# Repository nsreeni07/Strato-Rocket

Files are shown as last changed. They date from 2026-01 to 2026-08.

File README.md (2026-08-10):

Description

Strato is my first mid-power rocket, built as an introduction to rocketry and aerospace engineering. It stands 1.1 meters tall, reaches about 560 meters in altitude, and travels up to Mach 0.4. The rocket includes onboard avionics for GPS tracking, altitude measurement, and flight video recording.

The flight computer is a LILYGO T-Beam (ESP32-based) that logs GPS and telemetry data. A BMP390 measures altitude throughout the flight. An ESP32-CAM with an OV2640 records onboard video. The rocket uses a 36-inch parachute deployed by a black powder charge for safe recovery.

How to Use

Before launch, assemble the motor, recovery system, and avionics. Power on the flight computer and confirm GPS lock and sensor readings. After launch, the system automatically records flight data and deploys the parachute at apogee. After landing, retrieve the rocket and download the recorded data and video.

Why I Made This Project

I built Strato to begin my journey into rocketry and aerospace engineering. I wanted hands-on experience with avionics, sensors, telemetry, and recovery systems. This project helped me develop practical engineering skills and build a foundation for more advanced rockets in the future.

IMG_0525 (1)







|Category |Name |Price |Source |Purpose |FIELD6|Quantity|FIELD8|
|---|---|---|---|---|---|---|---|
|Electronics |LILYGO T-Beam V1.1(915mhz)|$66.64|https://lilygo.cc/en-us/products/t-beam?variant=51708943335605 |1 for rocket, 1 for ground tracking. | |2 | |
| |ESP32-CAM + Antenna |$5.82 |https://www.aliexpress.us/item/3256808866325459.html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 |The camera Board | |1 | |
| |OV2640 Camera |$4.23 |https://www.aliexpress.us/item/3256802853835121.html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 |To record the flight | |1 | |
| |MicroSD Card (32GB) |$3.55 |https://www.aliexpress.us/item/3256806229393591.html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 |Store Flight Video | |1 | |
| |BMP390 |$3.45 |https://www.aliexpress.us/item/2255800994181054.html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 |To measure altitude. | |1 | |
| |18650 Battery |$10.35|https://www.aliexpress.us/item/3256808362166008.html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 |Power for the rocket and ground station. | |1 | |
| |28 AWG Silicone Wire |$7.41 |https://www.aliexpress.us/item/3256808281675998.html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 |Vibration-proof wiring. | |1 |k |
| |Dupont Lines |$6.18 |https://www.aliexpress.com/item/3256806675662297.html |Breadboard Connector Wire | |1 | |
| | | | | | | | |
|Category |Name |Price |Source |Purpose | |Quantity| |
|Hardware |Epoxy |$3.48 |https://www.aliexpress.us/item/3256806928842047.html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|Adhesive | |2 | |
| |Recovery Wadding |$5.99 |https://estesrockets.com/products/recovery-wadding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 |Parachute Protection during ejection charge| |1 | |
| |Parachute Materials |$17.99|https://estesrockets.com/products/rip-stop-parachute?_pos=1&_sid=acb6b3712&_ss=r&variant=51539308052785 |Brings Rocket down safely | |1 | |
| |M6 Eye Bolts 30mm |$0.99 |https://www.aliexpress.us/item/3256803591110349.html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 |For attaching Shock cords to main Body | |1 | |
| |M6 Nylon Hex Spacers |$0.99 |https://www.aliexpress.us/item/2251832781404540.html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 |To Seperate wires and PCBS | |1 | |
| |Main Body Tube |$16.38|https://locprecision.com/products/slotted-cardboard-airframes?variant=39778658582719 |Body Tube | |1 | |
| |Shock Cord |$9.15 |https://locprecision.com/products/shock-cords?variant=39778658058431 |Absorbs shock | |1 | |
| |Mounting Tube |$2.25 |https://locprecision.com/products/motor-mount-tubing?variant=39778656813247 |Hold engine | |1 | |
|Category |Name |Price |Source |Purpose | |Quantity| |
|Self-Bought |G78G-7 |$0.00 |Buying Myself |Rocket Motor | |1 | |
| |Solder |$0.00 |Buying Myself |To solder wires to Avionics | |1 | |
| |3d Printed Nose Cone |$0.00 |Buying Myself |Nose Cone | |1 | |
| |3d Avionics Bay |$0.00 |Buying Myself |Hold Electronics | |1 | |
| |Spray Paint |$0.00 |Buying Myself |To Paint Rocket | |1 | |
| |PVC 5-Way |$0.00 |Buying Myself |For Rocket Launch Stand | |1 | |
| |Wood Filler |$9.99 |https://www.amazon.com/gp/product/B07JPB64XH/ref=ewc_pr_img_1?smid=A3I7U6FHIJ15X2&psc=1 |To thicken Epoxy | |1 | |
| |Balsa Wood |$7.99 |https://www.amazon.com/gp/product/B096P4G1RR/ref=ewc_pr_img_8?smid=A3BTZYV8IYFCZ9&th=1 |To Make Engine Centering Rings and Fins | |1 | |
| | | | | | | | |
| | | | | | | | |
| | | | | | | | |
| | | | | | | | |
| | | | | | | | |
| | | | | | | | |
| | | | | | | | |
| | | | | | | | |
| | | | | | | | |
| | | | | | | | |
|Below Totals contain Tax and Shipping | | | | | | | |
| | | | | | | | |
|Lilygo Total |$82.64 | | | | | | |
|Aliexpress Total |$51.59 | | | | | | |
|Amazon Total |$0.00 | | | | | | |
|LOC Total |$40.99 | | | | | | |
|Estes Total |$33.07 | | | | | | |
| | | | | | | | |
| | | | | | | | |
|Grant Total: |$208.29 | | | | | | |

[Strato BOM - Sheet1 (3).csv](https://github.com/user-attachments/files/25199135/Strato.BOM.-.Sheet1.3.csv)

# Strato-Rocket
https://docs.google.com/spreadsheets/d/1U2yEqBZTKHJVJrxIfUGXRck5QNupb0Gcpo2Jn2H-yjM/edit?usp=sharing

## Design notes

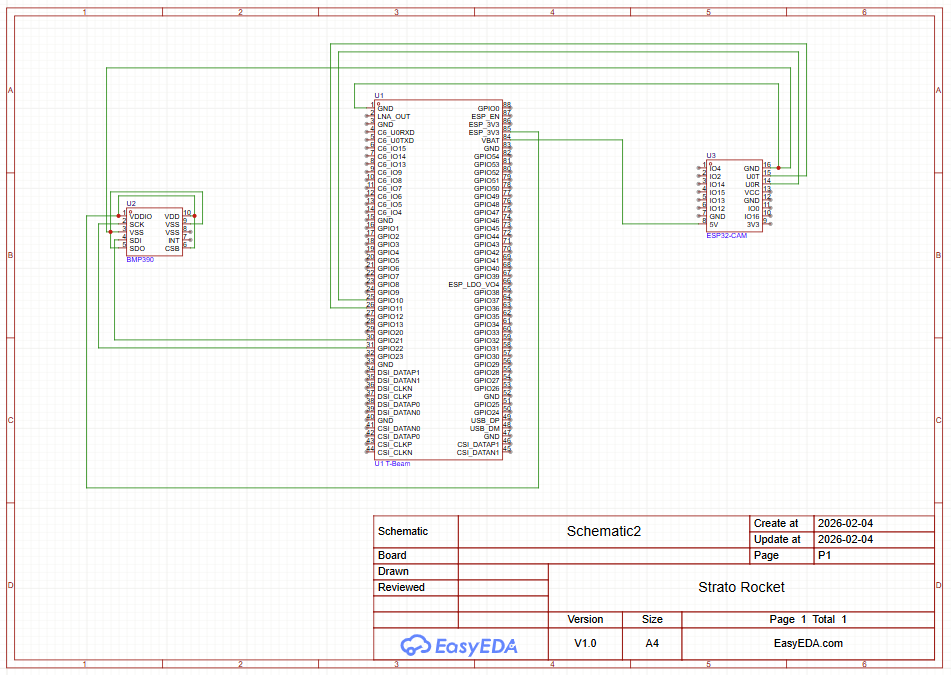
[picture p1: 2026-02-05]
Design Files/Strato-Avionics-Schematic.png

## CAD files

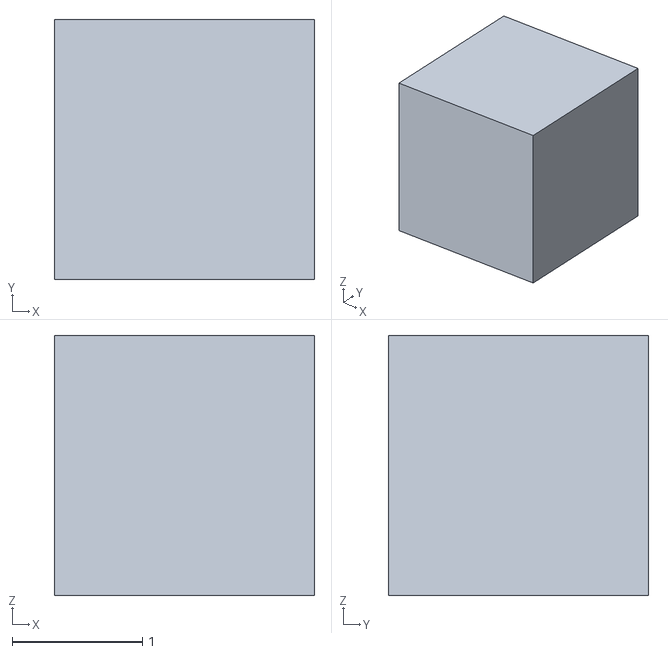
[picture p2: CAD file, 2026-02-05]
CAD Model/Final-AvionicsBay-RocketV7.stl
2.00 x 2.00 x 2.00

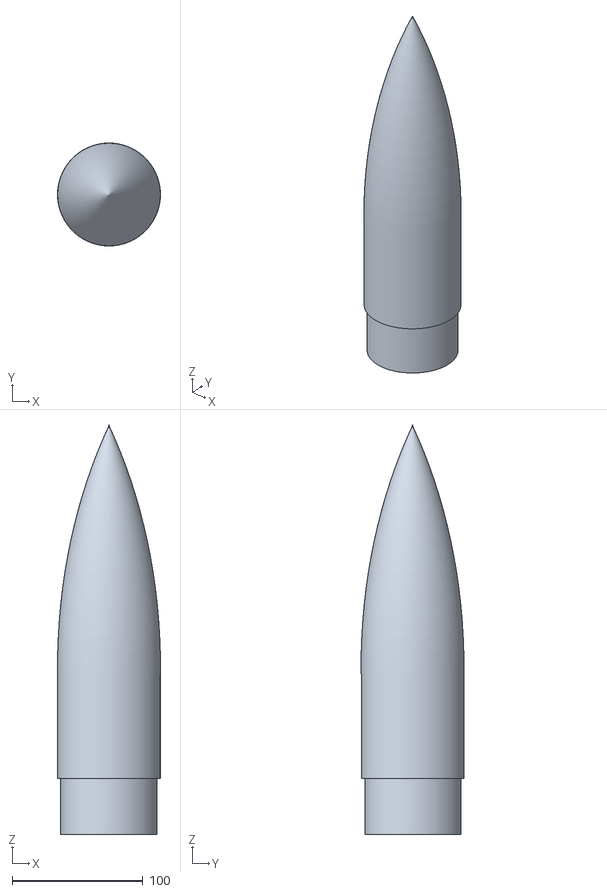
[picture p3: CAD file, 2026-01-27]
CAD Model/Final-NoseCone-RocketV7.stl
78.7 x 78.7 x 312.8

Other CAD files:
CAD Model/Final-AvionicsBay-RocketV7.blend

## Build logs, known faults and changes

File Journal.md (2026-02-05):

1/21

OpenRocket Model

So I worked on creating a rough idea of my rocket in OpenRocket, I reasearched through nose cone shapes and fin shapes to find the best one and finalized them into OpenRocket after around 2 hours, I have to start reasearching on avionics

3d CAD nose cone
I finished the 3d model for my Nose cone and started reasearching on how to design an proper avionic bay for my rocket. I've also started reasearch on an GPS made of Arduino Nano.

1/22

Reasearched Avionics Components

I reasearched on how to build my own avionics and what to put in it, 
I decided with using a LILYGO TTGO T-Beam (v1.1) and solder a BMP280 Barometric Sensor to track altitude, The LILYGO board will also be used to track GPS location to find the rocket after it lands, Im planning to also add a beeper but im not sure yet.
Im also going to connect an ESP32-Cam to a shared power rail to reduce weight of more parts, I'm still working on the final schematic for this whole avionics after which I will 3d design a CAD avionics bay.



1/23

Avionics Schematic

So, today I drew a schematic for my avionics it took a while to fully understand everything but after I did I was able to draw this sketch to how the wires will be soldered when I get them. The black wires are Ground for alitmeter and Camera, the 2 red wires sned power to the altimeter and camera, freen sends altiude data, and the Blue wire is the timing for the data. I'm going to reasearch more into how I can maximize these boards to get more data.  


I'm almost done with my avionics bay, I'm going to make a render of how it will all look soon ,I also gotta refresh on soldering because it has been a long time since I last did. 

1/24

3d CAD Avionics Bay

Today I made some good progress by finishing the Avionics bay, Instead of starting from scratch I found a similar avionics CAD model in thingiverse and i modified it to my needed specs. It took some trial and error, but it was satisfying to see the whoel thing come together nicely.  

While doing this I realized that the ESP-32 Camera I was planning to buy runs on 2.8v instead of the 3.3v i taught it ran on. The camera on the baord is a OV3660 which runs on 2.8V not 3.3V, because of this it could cause to board to overheat without proper ventialtion, I initally though to make a built in fan but that would take up space and weight. So I found a workaround by purchasing and 0V2640 camera on Aliexpress I can swap them to make the voltages match.

1/25

Rocket Rework and Fin Design Reasearch

So just some basic reasearch today, I extended the rocket to 110 cm, I went with the clipped delta shape for my fins but im still deciding between that or I make my own custom shape because I need to cut the corner of the fins so that when the rockets lands it wont land on the fin snapping it. I'm most likely going to design my own but we'll see.

Today was a small day but I going to focus on finalizing everything and making a rendering of the rocket with the livery and finish my BOM so I can get my project reviewed. 

1/26

Full Rocket 3d CAD model

So I made a full 3d CAD model of my Strato Rocket today, and I realized while making this that after I had updated the dimensions of my rocket in my previous journal I hadn't updated my older files containing my nose cone and Avionics Bay, So I went back and changed all the dimensions to match up correctly to make sure nothing wrogn happens during the printing process. I decided that my livery is going to be blue and white and I have to work on the rendering. 


I also updated my BOM for when I submit this design, I'm probably going to do a bit more reasearcha dn refine everything and finish my Github repository by uploading all my files and I should be good to submit for a grant. I totaled the costs and right now and its coming in tier 2 but it probably might go up a little but we will just have to see! 

1/27

Finished up BOM and livery 

So I finished up my BOM today and added up the costs and it is coming close to 300 but I know some areas where I can reduce costs. I also worked on my github finished my README.md and Journal.md and I just have to add images and my 3d models, For some reason github didnt let me upload my avionics bay 3d model even though the nose cone stl file upload just fine which was kinda weird but I solved the issue. I also finished my livery today the whole rocket primarily is Blue and White and this is just a basic idea for the livery I think I'll make some mods to it when the time comes to really paint it.



2/4
So I had to redesign my rocket and reduce more costs on my BOM. I managed to remove my rail guide after emailing some clubs who would allow me to launch using their equipment which is nice of them. Also I redesigned my rocket and brought the stability to around 2 because previously it was at 3.47 which is over-stable. While over stable sounds good the rocket could sometimes turn aggresively towards the wind on launch day reduicing altidude or the rocket breaking apart due to high g's. I could have done several things to bring it to 2.0 cal but I first reduced the heigh to 105cm and I brought the trailing edges of the fin upwarda and more close to the body this helped make the rocket come to around 2.05 cal where I wanted it to be for a safe stable flight. Because of this my calculated altidude has gone up to 559m. Im



I also made a proper avionics schematic, My previous one was on paper and hand-drawn and turns out had some flaws so I used EASYEDA and made an online schematic, This one is more proffesional and easier to vizualize. It took some time to figure out the whole website because it was my first time but I learned pretty quickly! Im going to submit for a re-design review so we will see what happens!


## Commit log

2026-01-27 Rename FinalStratoAvionicsBay.stl to CAD Models/FinalStratoAvionicsBay.stl
    [FinalStratoAvionicsBay.stl]
2026-01-27 Rename FinalStratoNoseCone.stl to CAD Models/FinalStratoNoseCone.stl
    [FinalStratoNoseCone.stl]
2026-01-29 Update Strato BOM - Sheet1.csv
    [Strato BOM - Sheet1.csv]
2026-01-30 Update and rename Strato BOM - Sheet1.csv to Design Files/Strato BOM - Sheet1.csv
    [Strato BOM - Sheet1.csv]
2026-01-31 Rename IMG_0142.jpeg to Avionics Schematic
2026-02-05 Rename Final-Strato-Rocket.stl to CAD Model/ Final-Strato-Rocket.stl
    [Final-Strato-Rocket.stl, Final-Strato-Rocket.stl]
